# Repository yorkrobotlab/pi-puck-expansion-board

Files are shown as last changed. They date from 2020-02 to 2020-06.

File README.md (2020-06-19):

# YRL Expansion Board for the Pi-puck

**An expansion board for the Pi-puck robot platform, including an IMU, XBee socket, navigation switch, RGB LED, and 24-pin Raspberry Pi compatible header.**

See https://github.com/yorkrobotlab/pi-puck for more information on the Pi-puck.

## PCB Layout

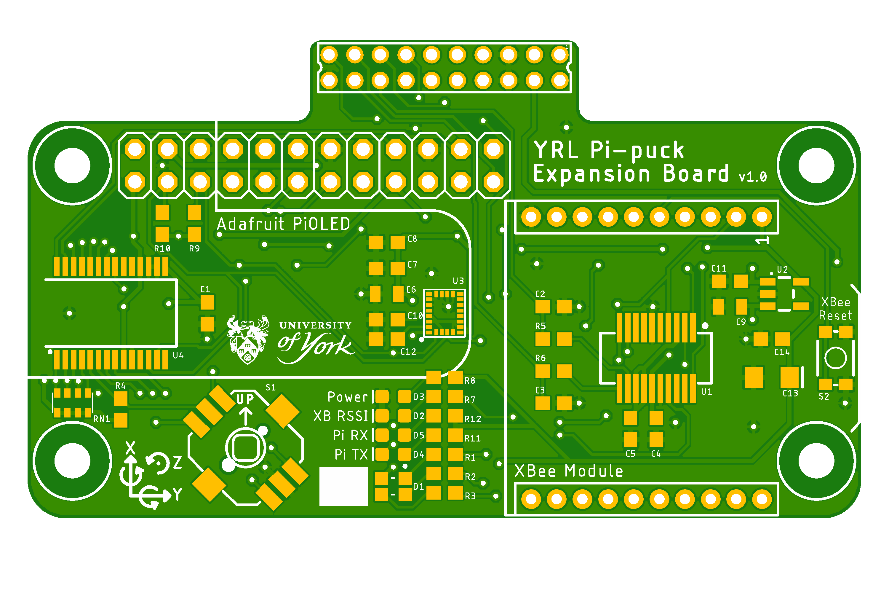
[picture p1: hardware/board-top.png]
PCB top


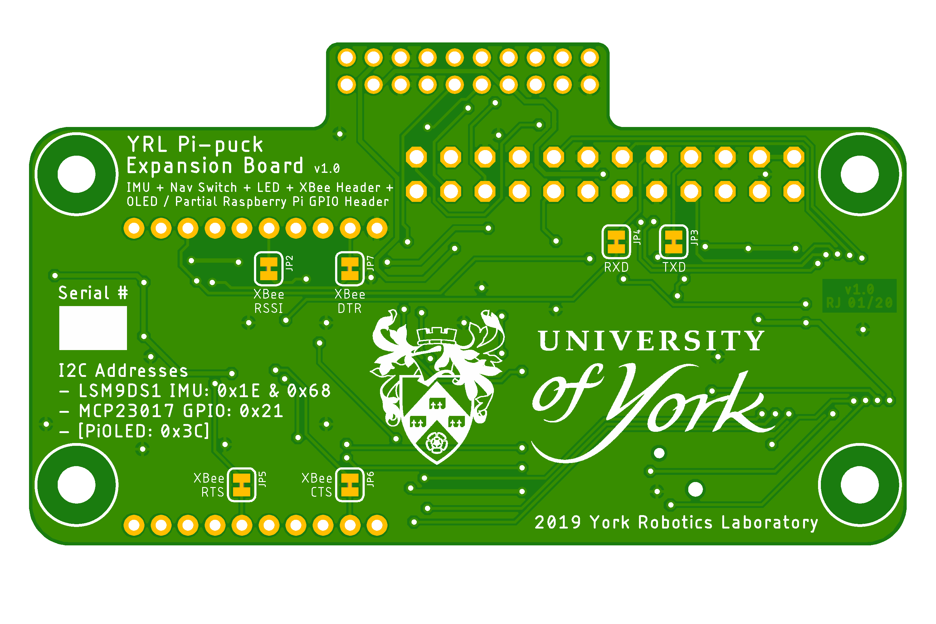
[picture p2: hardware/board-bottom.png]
PCB bottom


## XBee

Scripts to set up the XBee hardware and update the firmware are in [xbee/](xbee/).
Requires the Digi XBee Python Library (see https://github.com/digidotcom/xbee-python).

## Licence

Hardware designs are licensed under a [Creative Commons Attribution-ShareAlike 4.0 International Licence][cc-by-sa].

Unless otherwise specified, software is licensed under an [MIT Licence][mit].

[cc-by-sa]: http://creativecommons.org/licenses/by-sa/4.0/
[mit]: /LICENSE-MIT

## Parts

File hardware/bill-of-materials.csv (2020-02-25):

Part | Value | Description | Package | Manufacturer | Manufacturer Part Number | Supplier | Order code | Notes | URL
C2 | 47p | Capacitor | 0603 | KEMET | C0603X470J1GACTU | Farnell | 2905080 | ±5% C0G / NP0 | https://uk.farnell.com/kemet/c0603x470j1gactu/cap-47pf-100v-5-c0g-np0-0603/dp/2905080
C3 | 47p | Capacitor | 0603 | KEMET | C0603X470J1GACTU | Farnell | 2905080 | ±5% C0G / NP0 | https://uk.farnell.com/kemet/c0603x470j1gactu/cap-47pf-100v-5-c0g-np0-0603/dp/2905080
C10 | 10n | Capacitor | 0603 | KEMET | C0603X103J8JACTU | Farnell | 2579112 | ±5% U2J | http://uk.farnell.com/kemet/c0603x103j8jactu/capacitor-mlcc-u2j-0-01uf-10v/dp/2579112
C1 | 0.1u | Capacitor | 0603 | KEMET | C0603X104K8RACTU | Farnell | 2904937 | ±10% X7R | https://uk.farnell.com/kemet/c0603x104k8ractu/cap-0-1-f-10v-10-x7r-0603/dp/2904937
C4 | 0.1u | Capacitor | 0603 | KEMET | C0603X104K8RACTU | Farnell | 2904937 | ±10% X7R | https://uk.farnell.com/kemet/c0603x104k8ractu/cap-0-1-f-10v-10-x7r-0603/dp/2904937
C5 | 0.1u | Capacitor | 0603 | KEMET | C0603X104K8RACTU | Farnell | 2904937 | ±10% X7R | https://uk.farnell.com/kemet/c0603x104k8ractu/cap-0-1-f-10v-10-x7r-0603/dp/2904937
C7 | 0.1u | Capacitor | 0603 | KEMET | C0603X104K8RACTU | Farnell | 2904937 | ±10% X7R | https://uk.farnell.com/kemet/c0603x104k8ractu/cap-0-1-f-10v-10-x7r-0603/dp/2904937
C8 | 0.1u | Capacitor | 0603 | KEMET | C0603X104K8RACTU | Farnell | 2904937 | ±10% X7R | https://uk.farnell.com/kemet/c0603x104k8ractu/cap-0-1-f-10v-10-x7r-0603/dp/2904937
C11 | 0.1u | Capacitor | 0603 | KEMET | C0603X104K8RACTU | Farnell | 2904937 | ±10% X7R | https://uk.farnell.com/kemet/c0603x104k8ractu/cap-0-1-f-10v-10-x7r-0603/dp/2904937
C12 | 0.1u | Capacitor | 0603 | KEMET | C0603X104K8RACTU | Farnell | 2904937 | ±10% X7R | https://uk.farnell.com/kemet/c0603x104k8ractu/cap-0-1-f-10v-10-x7r-0603/dp/2904937
C14 | 0.1u | Capacitor | 0603 | KEMET | C0603X104K8RACTU | Farnell | 2904937 | ±10% X7R | https://uk.farnell.com/kemet/c0603x104k8ractu/cap-0-1-f-10v-10-x7r-0603/dp/2904937
C6 | 10u | Capacitor | 0805 | KEMET | C0805C106K8PACTU | Farnell | 1463362 | ±10% X5R | https://uk.farnell.com/kemet/c0805c106k8pactu/cap-10-f-10v-10-x5r-0805/dp/1463362
C9 | 10u | Capacitor | 0805 | KEMET | C0805C106K8PACTU | Farnell | 1463362 | ±10% X5R | https://uk.farnell.com/kemet/c0805c106k8pactu/cap-10-f-10v-10-x5r-0805/dp/1463362
C13 | 10u | Tantalum Capacitor | 1206 (EIA 3216–18) | KEMET | T491A106K016AT | Farnell | 1457414 | ±10% 16V | https://uk.farnell.com/kemet/t491a106k016at/cap-10-f-16v-10-1206-smd/dp/1457414
R5 | 27 | Resistor | 0603 | Panasonic | ERJ3GEYJ270V | Farnell | 2059559 |  | https://uk.farnell.com/panasonic/erj3geyj270v/res-27r-5-0-1w-0603-thick-film/dp/2059559
R6 | 27 | Resistor | 0603 | Panasonic | ERJ3GEYJ270V | Farnell | 2059559 |  | https://uk.farnell.com/panasonic/erj3geyj270v/res-27r-5-0-1w-0603-thick-film/dp/2059559
R1 | 1k | Resistor | 0603 | Panasonic | ERJ3GEYJ102V | Farnell | 2059601 |  | https://uk.farnell.com/panasonic/erj3geyj102v/res-1k-5-0-1w-0603-thick-film/dp/2059601
R2 | 1k | Resistor | 0603 | Panasonic | ERJ3GEYJ102V | Farnell | 2059601 |  | https://uk.farnell.com/panasonic/erj3geyj102v/res-1k-5-0-1w-0603-thick-film/dp/2059601
R3 | 1k | Resistor | 0603 | Panasonic | ERJ3GEYJ102V | Farnell | 2059601 |  | https://uk.farnell.com/panasonic/erj3geyj102v/res-1k-5-0-1w-0603-thick-film/dp/2059601
R7 | 1k | Resistor | 0603 | Panasonic | ERJ3GEYJ102V | Farnell | 2059601 |  | https://uk.farnell.com/panasonic/erj3geyj102v/res-1k-5-0-1w-0603-thick-film/dp/2059601
R8 | 1k | Resistor | 0603 | Panasonic | ERJ3GEYJ102V | Farnell | 2059601 |  | https://uk.farnell.com/panasonic/erj3geyj102v/res-1k-5-0-1w-0603-thick-film/dp/2059601
R11 | 1k | Resistor | 0603 | Panasonic | ERJ3GEYJ102V | Farnell | 2059601 |  | https://uk.farnell.com/panasonic/erj3geyj102v/res-1k-5-0-1w-0603-thick-film/dp/2059601
R12 | 1k | Resistor | 0603 | Panasonic | ERJ3GEYJ102V | Farnell | 2059601 |  | https://uk.farnell.com/panasonic/erj3geyj102v/res-1k-5-0-1w-0603-thick-film/dp/2059601
R9 | 4.7k | Resistor | 0603 | Panasonic | ERJ3GEYJ472V | Farnell | 2059619 |  | https://uk.farnell.com/panasonic/erj3geyj472v/res-4k7-5-0-1w-0603-thick-film/dp/2059619
R10 | 4.7k | Resistor | 0603 | Panasonic | ERJ3GEYJ472V | Farnell | 2059619 |  | https://uk.farnell.com/panasonic/erj3geyj472v/res-4k7-5-0-1w-0603-thick-film/dp/2059619
R4 | 10k | Resistor | 0603 | Panasonic | ERJ3GEYJ103V | Farnell | 2059627 |  | http://uk.farnell.com/panasonic-electronic-components/erj3geyj103v/res-thick-film-10k-5-0-1w-0603/dp/2059627
RN1 | 10k | Array Chip Resistor | EXBV8V | Panasonic | EXBV8V103JV | Farnell | 2060167 |  | https://uk.farnell.com/panasonic/exbv8v103jv/resistor-ccav-array-0603x4-10k/dp/2060167
D3 |  | Red LED | 0603 | Kingbright | KPT-1608LVSECK-J3-PRV | Farnell | 2610406 |  | https://uk.farnell.com/kingbright/kpt-1608lvseck-j3-prv/led-red-40mcd-625nm-smd/dp/2610406
D5 |  | Red LED | 0603 | Kingbright | KPT-1608LVSECK-J3-PRV | Farnell | 2610406 |  | https://uk.farnell.com/kingbright/kpt-1608lvseck-j3-prv/led-red-40mcd-625nm-smd/dp/2610406
D4 |  | Green LED | 0603 | Kingbright | KPT-1608LVZGCK | Farnell | 2610409 |  | https://uk.farnell.com/kingbright/kpt-1608lvzgck/led-green-50mcd-525nm-smd/dp/2610409
D2 |  | Blue LED | 0603 | Kingbright | KPT-1608LVVBC-D | Farnell | 2610410 |  | https://uk.farnell.com/kingbright/kpt-1608lvvbc-d/led-blue-24mcd-470nm-smd/dp/2610410
D1 |  | RGB LED | 0805 | Würth Elektronik | 150080M153000 | Farnell | 2764966 |  | https://uk.farnell.com/wurth-elektronik/150080m153000/led-red-grn-blue-112-285-70mcd/dp/2764966
S1 |  | Small Tactile Joystick w/ Select Switch | SMD with guide bosses | Multicomp | MCMT5-F-V | Farnell | 1316987 |  | https://uk.farnell.com/multicomp/mcmt5-f-v/navigation-switch-5way-smd/dp/1316987
S2 |  | Momentary Switch (Pushbutton) - SPST | KMR2 (SMD 4.6x2.8mm) | C & K Components | KMR221NG LFS | Farnell | 2845727 | Maybe change to grounded version next time | https://uk.farnell.com/c-k-components/kmr221ng-lfs/tactile-sw-spst-no-0-05a-32vdc/dp/2845727
U1 |  | FT231X USB-UART Converter | SSOP-20 | FTDI | FT231XS-R | Farnell | 2081328 |  | https://uk.farnell.com/ftdi/ft231xs/i-f-usb2-0-fs-to-f-l-h-s-uart/dp/2081328
U2 |  | 3.3V voltage regulator | SOT23-5 | Microchip | MIC5219-3.3YM5-TR | Farnell | 2510252 |  | https://uk.farnell.com/microchip/mic5219-3-3ym5-tr/ldo-0-5vdo-0-5a-3-3v-1-5sot23/dp/2510252
U3 |  | LSM9DS1 9DoF IMU | LGA-24 | ST Microelectronics | LSM9DS1TR | Farnell | 2532383 |  | https://uk.farnell.com/stmicroelectronics/lsm9ds1tr/mems-accelero-gyroscope-magneto/dp/2532383
U4 |  | I2C 16-bit GPIO Expander | SSOP-28 | Microchip | MCP23017-E/SS | Farnell | 1467674 | On schematic as MCP23017SS | http://uk.farnell.com/microchip/mcp23017-e-ss/ic-io-expander-16bit-smd/dp/1467674

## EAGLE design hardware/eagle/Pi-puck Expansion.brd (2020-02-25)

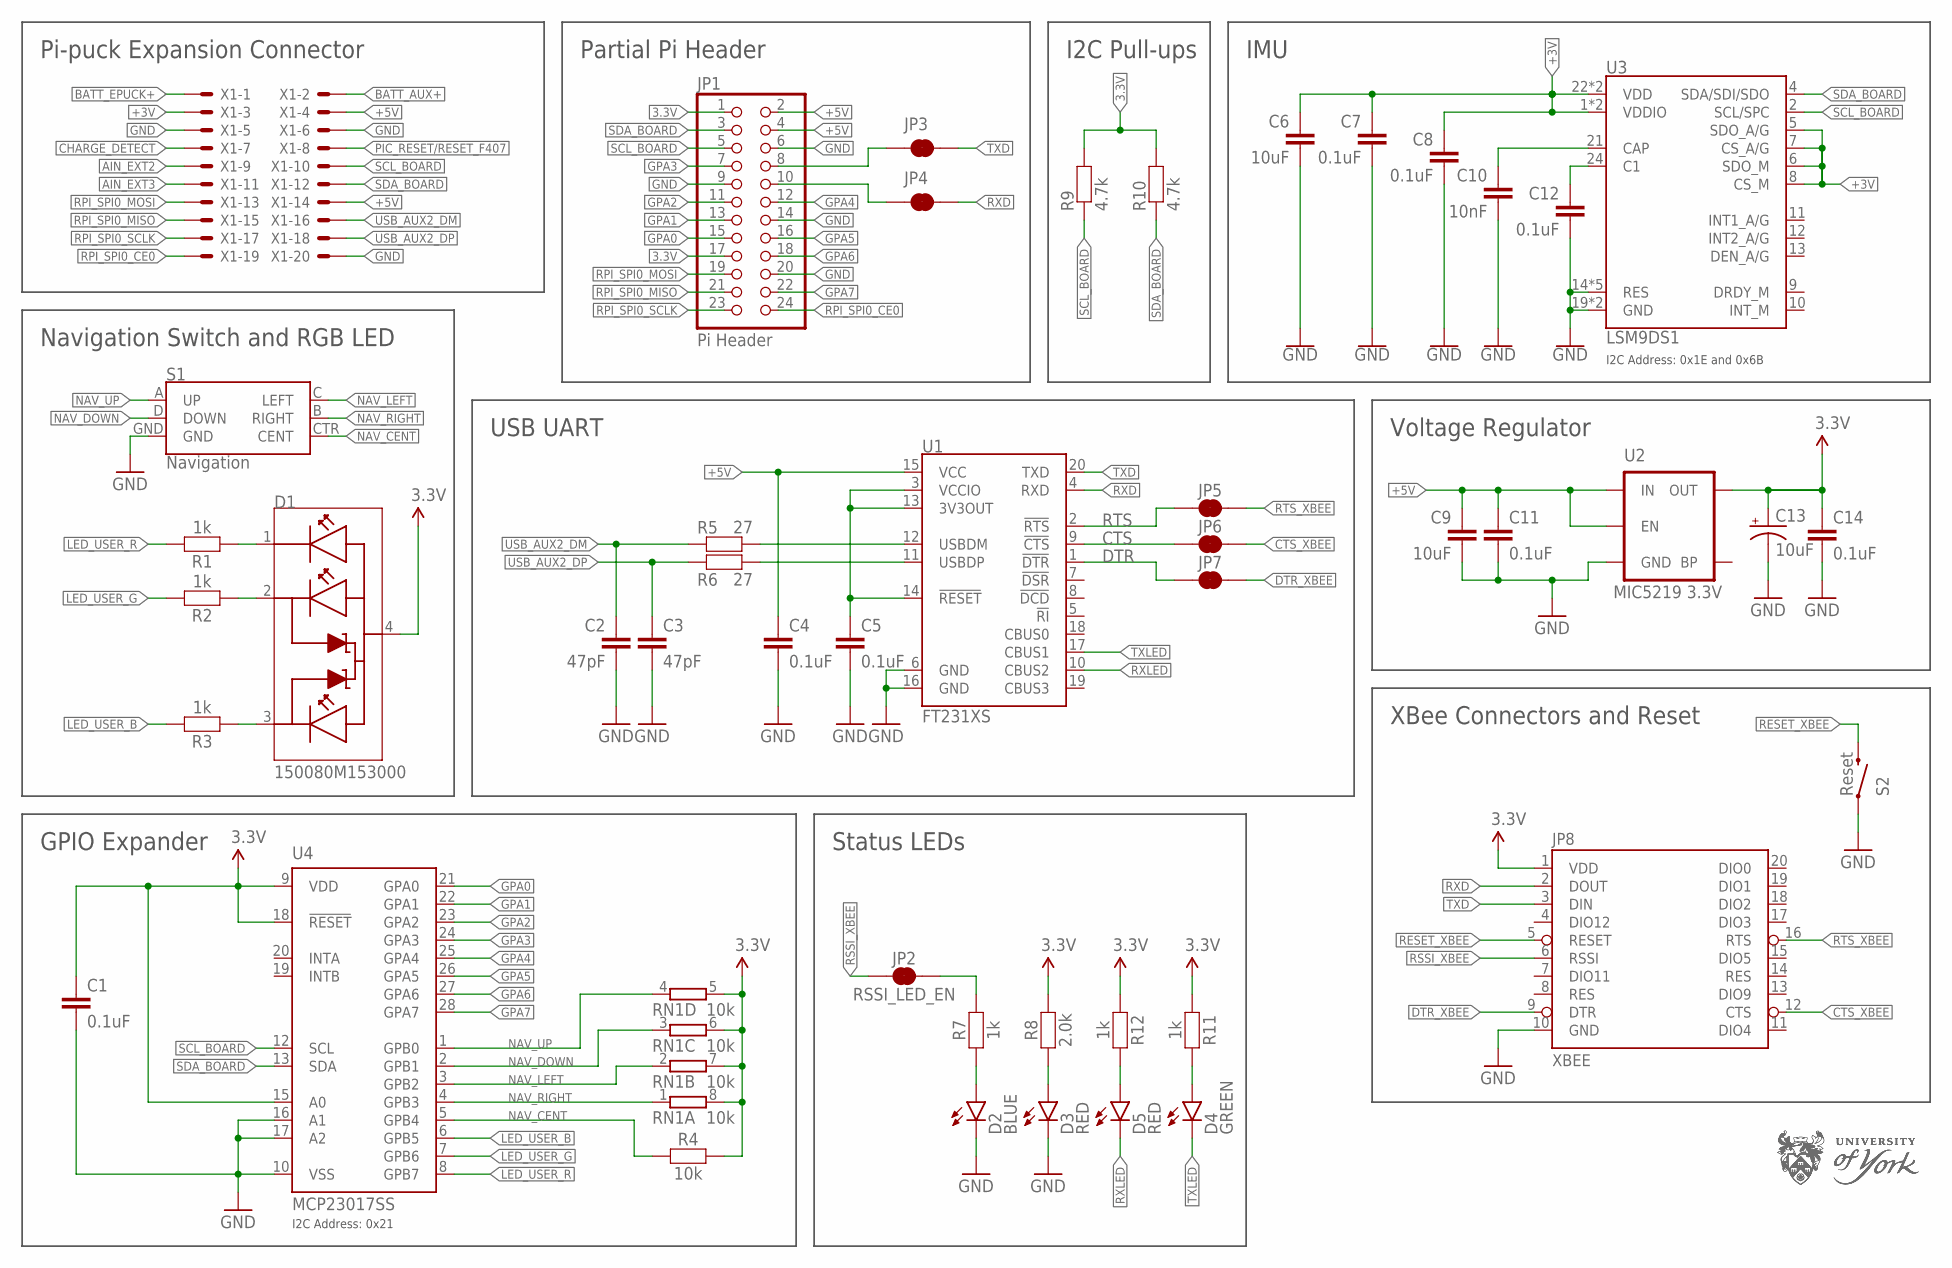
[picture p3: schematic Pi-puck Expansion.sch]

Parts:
C1, C4, C5, C7, C8, C11, C12, C14: 0.1uF; 0603
C2, C3: 47pF; 0603
C6, C9: 10uF; 0805
C10: 10nF; 0603
C13: 10uF; EIA3216
D1: 150080M153000; LED_150080M153000
D2: BLUE; LED-0603
D3, D5: RED; LED-0603
D4: GREEN; LED-0603
JP1: Pi Header; 2X12
JP2: RSSI_LED_EN; SMT-JUMPER_2_NC_TRACE_SILK
JP3: TXD; SMT-JUMPER_2_NC_TRACE_SILK
JP4: RXD; SMT-JUMPER_2_NC_TRACE_SILK
JP5: CTS_EN; SMT-JUMPER_2_NC_TRACE_SILK
JP6: RTS_EN; SMT-JUMPER_2_NC_TRACE_SILK
JP7: DTR; SMT-JUMPER_2_NC_TRACE_SILK
JP8: XBEE; XBEE-SILK
LOGO1: UOY-LOGO-30MM; UOY-LOGO-30MM-WIDE
LOGO2: UOY-LOGO-10MM; UOY-LOGO-10MM-WIDE
R1, R2, R3, R7, R11, R12: 1k; 0603
R4: 10k; 0603
R5, R6: 27; 0603
R8: 2.0k; 0603
R9, R10: 4.7k; 0603
RN1: 10k; EXBV8V
S1: Navigation; JOYSTICK_MINI
S2: Reset; TACTILE_SWITCH_SMD_4.6X2.8MM
U1: FT231XS; SSOP20_L
U2: MIC5219 3.3V; SOT23-5
U3: LSM9DS1; LGA24-8X4
U4: MCP23017SS; SSOP28
X1: 87758-2016

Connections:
3.3V: C1.1, C13.+, C14.1, D1.4 (A), JP1.1, JP1.17, JP8.1 (VDD), R4.2, R8.2, R9.2, R10.2, R11.1, R12.1, RN1.5 (2), RN1.6 (2), RN1.7 (2), RN1.8 (2), U2.5 (OUT), U4.9 (VDD), U4.15 (A0), U4.18 (!RESET)
3V-INT: C5.1, U1.3 (VCCIO), U1.13 (3V3OUT), U1.14 (!RESET)
+3V: C6.1, C7.1, C8.1, U3.1 (VDDIO), U3.3 (VDDIO), U3.5 (SDO_A/G), U3.6 (SDO_M), U3.7 (CS_A/G), U3.8 (CS_M), U3.22 (VDD), U3.23 (VDD), X1.3
+5V: C4.1, C9.1, C11.1, JP1.2, JP1.4, U1.15 (VCC), U2.1 (IN), U2.3 (EN), X1.4, X1.14
AIN_EXT2: X1.9
AIN_EXT3: X1.11
BATT_AUX+: X1.2
BATT_EPUCK+: X1.1
C1: C12.1, U3.24 (C1)
CAP: C10.1, U3.21 (CAP)
CHARGE_DETECT: X1.7
CTS: JP6.1, U1.9 (!CTS)
CTS_XBEE: JP6.2, JP8.12 (CTS)
DTR: JP7.1, U1.1 (!DTR)
DTR_XBEE: JP7.2, JP8.9 (DTR)
GND: C1.2, C2.2, C3.2, C4.2, C5.2, C6.2, C7.2, C8.2, C9.2, C10.2, C11.2, C12.2, C13.-, C14.2, D2.C, D3.C, JP1.6, JP1.9, JP1.14, JP1.20, JP8.10 (GND), S1.GND, S2.1, S2.2 (1), U1.6 (GND), U1.16 (GND), U2.2 (GND), U3.14 (RES), U3.15 (RES), U3.16 (RES), U3.17 (RES), U3.18 (RES), U3.19 (GND), U3.20 (GND), U4.10 (VSS), U4.16 (A1), U4.17 (A2), X1.5, X1.6, X1.20
GPA0: JP1.15, U4.21 (GPA0)
GPA1: JP1.13, U4.22 (GPA1)
GPA2: JP1.11, U4.23 (GPA2)
GPA3: JP1.7, U4.24 (GPA3)
GPA4: JP1.12, U4.25 (GPA4)
GPA5: JP1.16, U4.26 (GPA5)
GPA6: JP1.18, U4.27 (GPA6)
GPA7: JP1.22, U4.28 (GPA7)
LED_USER_B: R3.2, U4.6 (GPB5)
LED_USER_G: R2.2, U4.7 (GPB6)
LED_USER_R: R1.2, U4.8 (GPB7)
unnamed: D5.A, R12.2
unnamed: JP1.8, JP3.1
unnamed: JP1.10, JP4.1
unnamed: D4.A, R11.2
unnamed: D1.1 (R), R1.1
unnamed: R6.2, U1.11 (USBDP)
unnamed: R5.2, U1.12 (USBDM)
unnamed: JP2.2, R7.2
unnamed: D1.2 (G), R2.1
unnamed: D1.3 (B), R3.1
unnamed: D3.A, R8.1
NAV_CENT: R4.1, S1.CTR (CENT), U4.5 (GPB4)
NAV_DOWN: RN1.3 (1), S1.D (DOWN), U4.2 (GPB1)
NAV_LEFT: RN1.2 (1), S1.C (LEFT), U4.3 (GPB2)
NAV_RIGHT: RN1.1, S1.B (RIGHT), U4.4 (GPB3)
NAV_UP: RN1.4 (1), S1.A (UP), U4.1 (GPB0)
PIC_RESET/RESET_F407: X1.8
RESET_XBEE: JP8.5 (RESET), S2.3 (2), S2.4 (2)
RPI_SPI0_CE0: JP1.24, X1.19
RPI_SPI0_MISO: JP1.21, X1.15
RPI_SPI0_MOSI: JP1.19, X1.13
RPI_SPI0_SCLK: JP1.23, X1.17
RSSILED: D2.A, R7.1
RSSI_XBEE: JP2.1, JP8.6 (RSSI)
RTS: JP5.1, U1.2 (!RTS)
RTS_XBEE: JP5.2, JP8.16 (RTS)
RXD: JP4.2, JP8.2 (DOUT), U1.4 (RXD)
RXLED: D5.C, U1.10 (CBUS2)
SCL_BOARD: JP1.5, R9.1, U3.2 (SCL/SPC), U4.12 (SCL), X1.10
SDA_BOARD: JP1.3, R10.1, U3.4 (SDA/SDI/SDO), U4.13 (SDA), X1.12
TXD: JP3.2, JP8.3 (DIN), U1.20 (TXD)
TXLED: D4.C, U1.17 (CBUS1)
USB_AUX2_DM: C2.1, R5.1, X1.16
USB_AUX2_DP: C3.1, R6.1, X1.18

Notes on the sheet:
Pi-puck Expansion Connector
Partial Pi Header
GPIO Expander
I2C Address: 0x21
Navigation Switch and RGB LED
I2C Address: 0x1E and 0x6B
Voltage Regulator
I2C Pull-ups
USB UART
IMU
XBee Connectors and Reset
Status LEDs

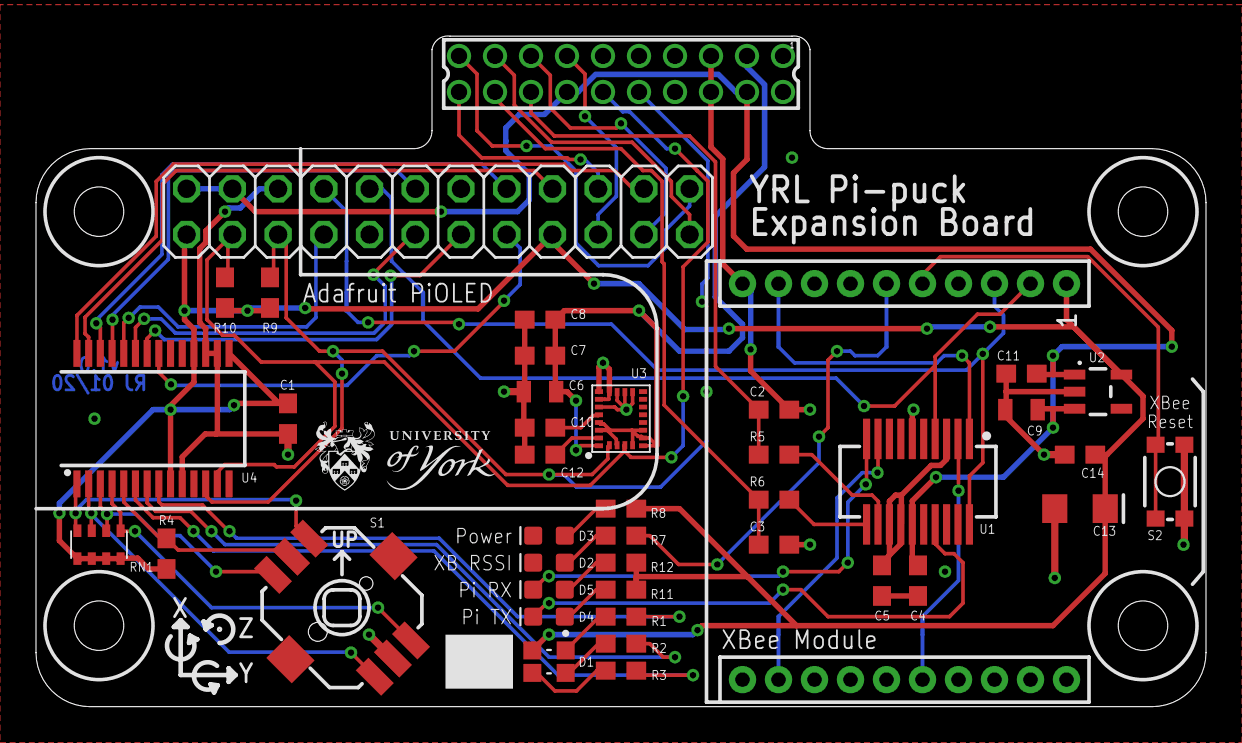
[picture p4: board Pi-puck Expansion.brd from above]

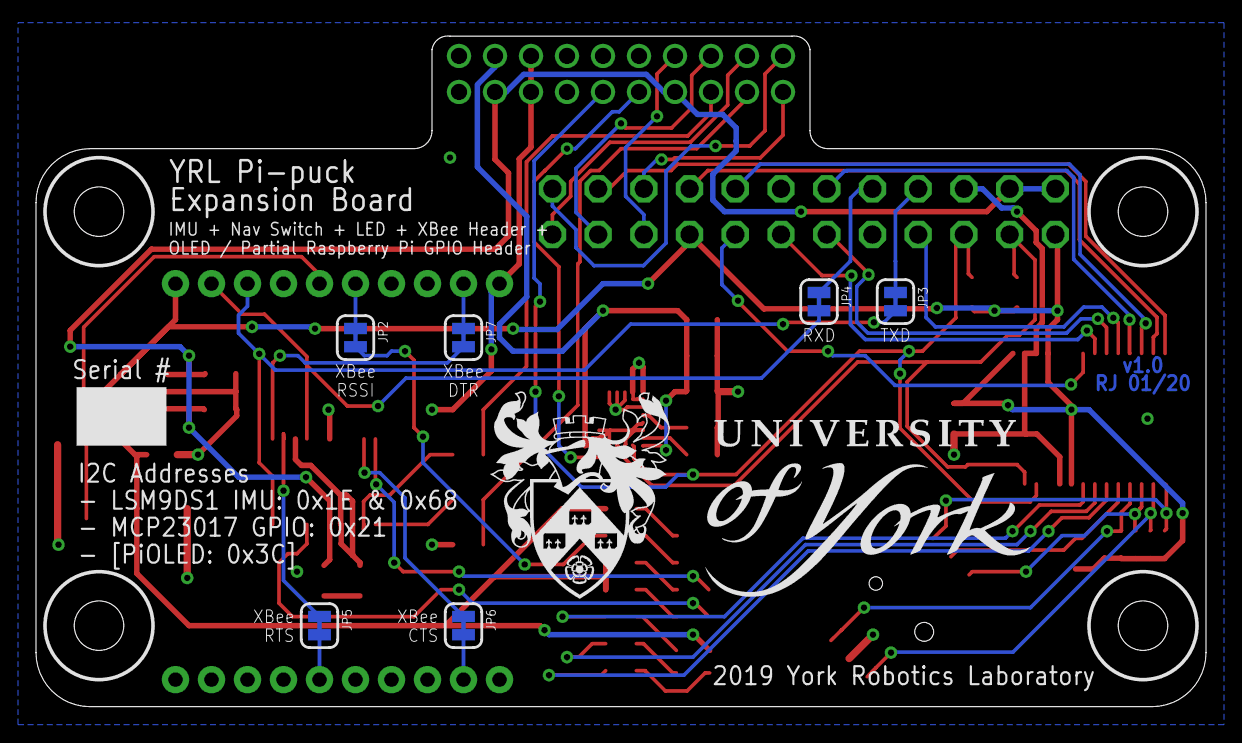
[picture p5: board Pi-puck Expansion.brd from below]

Board: 2 copper layers, 65.0 x 37.3 mm, 49 parts (7 on the bottom side), 55 nets.

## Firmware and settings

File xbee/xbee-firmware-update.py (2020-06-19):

#!/usr/bin/env python3

import argparse
import sys
from digi.xbee.devices import XBeeDevice
from digi.xbee.firmware import update_local_firmware
from digi.xbee.exception import FirmwareUpdateException, OperationNotSupportedException, XBeeException


def main():
	parser = argparse.ArgumentParser(description="XBee firmware update.")
	parser.add_argument("xml_firmware_file", type=str, help="XML firmware file")
	parser.add_argument("xbee_firmware_file", type=str, nargs='?', default=None, help="XBee firmware file")
	parser.add_argument("bootloader_firmware_file", type=str, nargs='?', default=None, help="bootloader firmware file")
	parser.add_argument("-p", "--port", type=str, default="/dev/ttyUSB0", help="serial port (default /dev/ttyUSB0)")
	parser.add_argument("-b", "--baud", type=int, default=9600, help="serial baud rate (default 9600)")
	parser.add_argument("-t", "--timeout", type=int, default=None, help="communication timeout (optional)")
	parser.add_argument("-s", "--serial", action="store_true", help="use raw serial mode instead of API mode")
	args = parser.parse_args()

	xml_firmware_file = args.xml_firmware_file
	xbee_firmware_file = args.xbee_firmware_file
	bootloader_firmware_file = args.bootloader_firmware_file
	port = args.port
	baud = args.baud
	timeout = args.timeout
	serial = args.serial

	if serial:
		device = None
	else:
		device = XBeeDevice(port, baud)

	try:
		print("Starting firmware update ...")
		if serial:
			update_local_firmware(port, xml_firmware_file,
			                      xbee_firmware_file=xbee_firmware_file,
			                      bootloader_firmware_file=bootloader_firmware_file,
			                      timeout=timeout,
			                      progress_callback=progress_callback)
		else:
			device.open()
			device.update_firmware(xml_firmware_file,
			                       xbee_firmware_file=xbee_firmware_file,
			                       bootloader_firmware_file=bootloader_firmware_file,
			                       timeout=timeout,
			                       progress_callback=progress_callback)
		print("Firmware update successful!")
	except (XBeeException, FirmwareUpdateException, OperationNotSupportedException) as e:
		print("Error: %s" % str(e))
		sys.exit(1)
	finally:
		if device is not None and device.is_open():
			device.close()


def progress_callback(task, percent):
	print("%s: %d%%" % (task, percent))


if __name__ == "__main__":
	main()

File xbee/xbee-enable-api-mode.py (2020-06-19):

#!/usr/bin/env python3

import serial
import sys
import time

print("Enabling API mode on XBee...")

ser = serial.Serial('/dev/ttyUSB0')

print()
time.sleep(1)
print("+++")
ser.write(b"+++")
time.sleep(1)
response = ser.read_until(b"\r")
print(response)
if response != b"OK\r":
    print("Error entering AT mode")
    sys.exit(1)

print()
print("ATAP 1<CR>")
ser.write(b"ATAP 1\r")
response = ser.read_until(b"\r")
print(response)
if response != b"OK\r":
    print("Error setting API mode")
    sys.exit(1)

print()
print("ATWR<CR>")
ser.write(b"ATWR\r")
response = ser.read_until(b"\r")
print(response)
if response != b"OK\r":
    print("Error writing data")
    sys.exit(1)

print()
print("ATCN<CR>")
ser.write(b"ATCN\r")
response = ser.read_until(b"\r")
print(response)
if response != b"OK\r":
    print("Error exiting command mode")
    sys.exit(1)

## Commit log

2020-02-25 Added hardware design, and some info into the readme file
    [Pi-Puck Expansion v1.0.brd, Pi-Puck Expansion v1.0.sch, bill-of-materials.csv]
2020-02-25 Updated PCB layout images to include ground planes
2020-02-25 Updated schematic PDF and renamed Eagle design files
    [Pi-puck Expansion.brd, Pi-puck Expansion.sch]

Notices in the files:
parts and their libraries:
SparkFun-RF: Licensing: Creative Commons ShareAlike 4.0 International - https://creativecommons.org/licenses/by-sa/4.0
